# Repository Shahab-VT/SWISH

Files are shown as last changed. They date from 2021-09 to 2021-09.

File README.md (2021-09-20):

# SWISH: A shifting-weight interface of simulated hydrodynamics for haptic perception of virtual fluid vessels

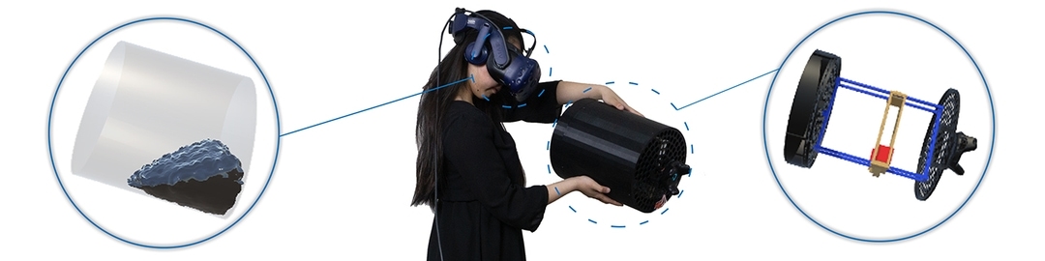
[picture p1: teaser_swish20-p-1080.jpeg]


Publication

Shahabedin Sagheb, Frank Wencheng Liu, Alireza Bahremand, Assegid Kidane, Robert LiKamWa
SWISH: A Shifting-Weight Interface of Simulated Hydrodynamics for Haptic Perception of Virtual Fluid Vessels
In Proceedings of UIST'19: https://dl.acm.org/doi/10.1145/3332165.3347870

Abstract

Current VR/AR systems are unable to reproduce the physical sensation of fluid vessels, due to the shifting nature of fluid motion. To this end, we introduce SWISH, 
an ungrounded mixed-reality interface, capable of affording the users a realistic haptic sensation of fluid behaviors in vessels.The chief mechanism behind SWISH 
is in the use of virtual reality tracking and motor actuation to actively relocate the center of gravity of a handheld vessel, emulating the moving center of 
gravity of a handheld vessel that contains fluid. In addition to solving challenges related to reliable and efficient motor actuation, our SWISH designs place 
an emphasis on reproducibility, scalability, and availability to the maker culture. Our virtual-to-physical coupling uses Nvidia Flex's Unity integration for 
virtual fluid dynamics with a3D printed augmented vessel containing a motorized mechanical actuation system.To evaluate the effectiveness and perceptual 
efficacy of SWISH, we conduct a user study with 24 participants, 7 vessel actions, and 2 virtual fluid viscosities in a virtual reality environment. 
In all cases, the users on average reported that the SWISH bucket generates accurate tactile sensations for the fluid behavior. This opens the potential for 
multi-modal interactions with programmable fluids in virtual environments for chemistry education, worker training, and immersive entertainment.

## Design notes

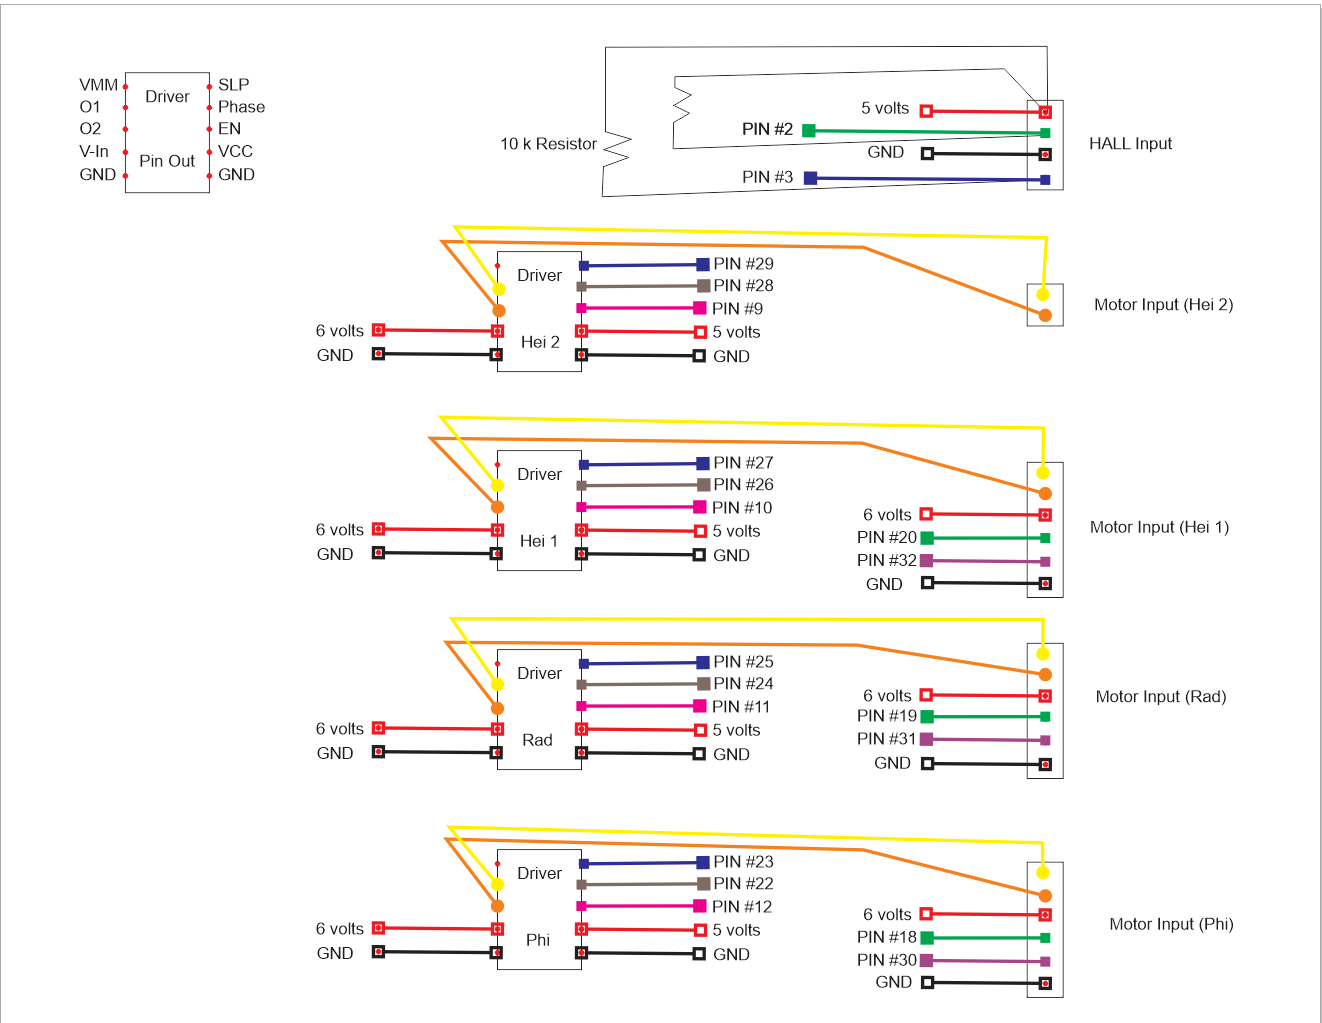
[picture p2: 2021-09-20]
Schematics/SWISH_PCB_1.PNG

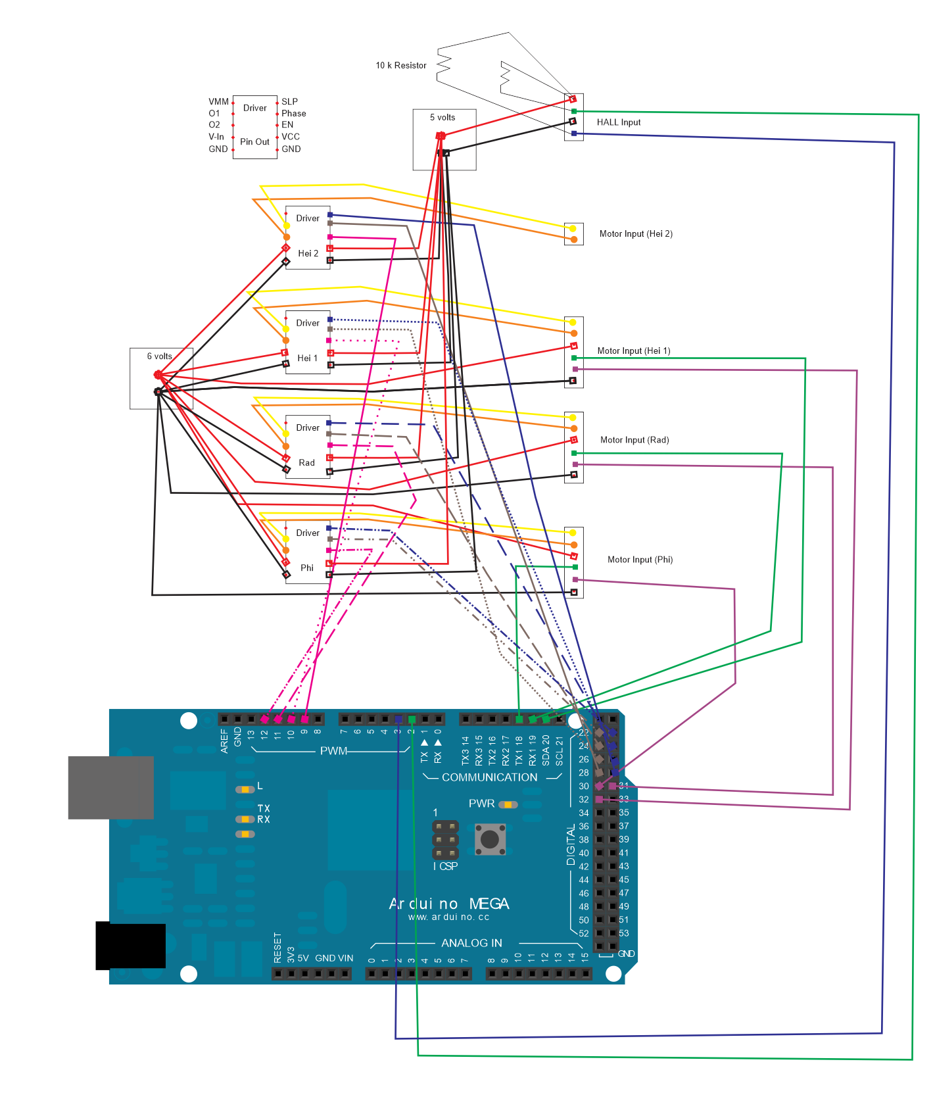
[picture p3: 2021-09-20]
Schematics/SWISH_PCB_2_Wires.PNG

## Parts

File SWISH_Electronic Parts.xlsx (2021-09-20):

Part | Model | Quantity | Link to purchase | Notes
DC Motor | 298:1 Micro Metal | 4 | Pololu - 298:1 Micro Metal Gearmotor HP 6V with Extended Motor Shaft (https://www.pololu.com/product/2218)
Magnetic Encoder |  | 4 | Pololu - Magnetic Encoder Pair Kit with Side-Entry Connector for Micro Metal Gearmotors, 12 CPR, 2.7-18V (https://www.pololu.com/product/4761)
6 Pin Cable | Female JST SH-Style Cable 12cm | 4 | Pololu - 6-Pin Single-Ended Female JST SH-Style Cable 12cm (https://www.pololu.com/product/4762)
Motor Driver | DRV8838 Single | 4 | Pololu - DRV8838 Single Brushed DC Motor Driver Carrier (https://www.pololu.com/product/2990)
Slip Ring | 12.5mm 18 Wires | 1 | Taidacent Small Slip Ring Conductive Ring Miniature Rotating Conductive Slip Ring 2 4 6 8 10 12 24 Road Cap Slip Ring (18 Wire 2A OD 22mm Metal) - - Amazon.com (https://www.amazon.com/Taidacent-Small-Conductive-Miniature-Rotating/dp/B07Y9MLRJN?s=hi) | Plastic one would do as well
Needle Roller Bearing | 1/2" ID, 11/16" OD, 3/8" Width | 1 | INA SCE86 Needle Roller Bearing, Steel Cage, Open End, Inch, 1/2" ID, 11/16" OD, 3/8" Width, 22000rpm Maximum Rotational Speed, 1210lbf Static Load Capacity, 1040lbf Dynamic Load Capacity: Amazon.com: Industrial & Scientific (https://www.amazon.com/gp/product/B00270U27C/ref=ppx_yo_dt_b_asin_title_o01_s00?ie=UTF8&psc=1)
Ball Bearing | R4-2RS (1/4"x5/8"x0.196") | 1 | (10 Pack) PGN - R4-2RS Sealed Ball Bearing - C3-1/4"x5/8"x0.196" - Lubricated - Chrome Steel: Amazon.com: Industrial & Scientific (https://www.amazon.com/PGN-R4-2RS-Sealed-Bearing-Lubricated/dp/B07GT739PV)
Hall-Effect Sensor | AH1815 (Non-Latching) | 2 | Hall-Effect Sensor - AH1815 (Non-Latching) - SEN-14709 - SparkFun Electronics (https://www.sparkfun.com/products/14709)
Set Screw | 1/4" 20 set screw | 1 | Hardware Store
Magnets | 1/4 inch | 2 | 1/4 Inch Neodymium Rare Earth Cube Magnets N52 (64 Pack) (totalelement.com) (https://totalelement.com/collections/cube-magnets/products/1-4-inch-neodymium-rare-earth-cube-magnets-n52-64-pack)
Male & Female Pin Headers |  | N/A | 80 Pieces Male and Female Pin Header Connector 40 Pin 2.54 mm Single Row Straight Pin for Arduino Shield: Amazon.com: Industrial & Scientific (https://www.amazon.com/gp/product/B07VNXL5BD/ref=ppx_yo_dt_b_asin_title_o06_s00?ie=UTF8&psc=1)
Heat Shrink |  | N/A

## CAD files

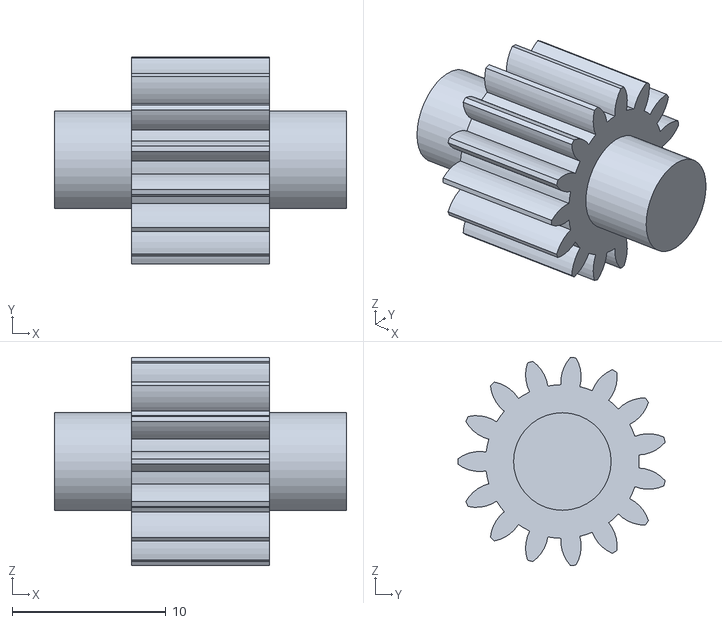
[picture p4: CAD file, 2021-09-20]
STL Files for printing/LASy_SW_spur_gear_Vert_4_Bottom.STL
19.0 x 13.5 x 13.6

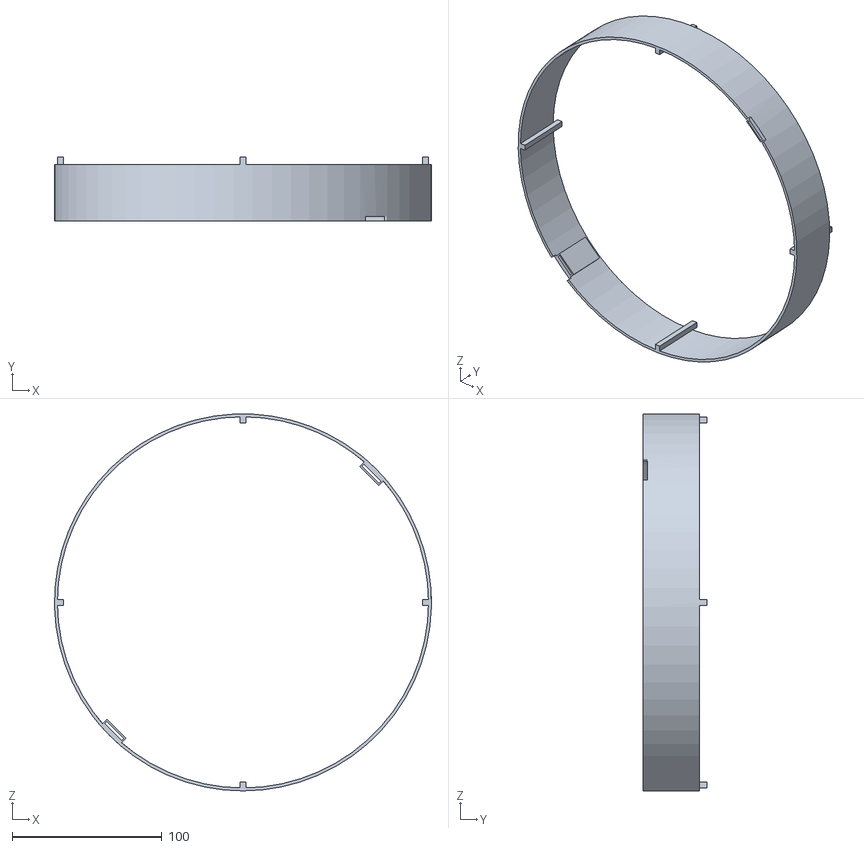
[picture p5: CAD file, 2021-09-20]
STL Files for printing/LASy_Bucket_Stand_3_WiSup.STL
252.0 x 43.0 x 251.8

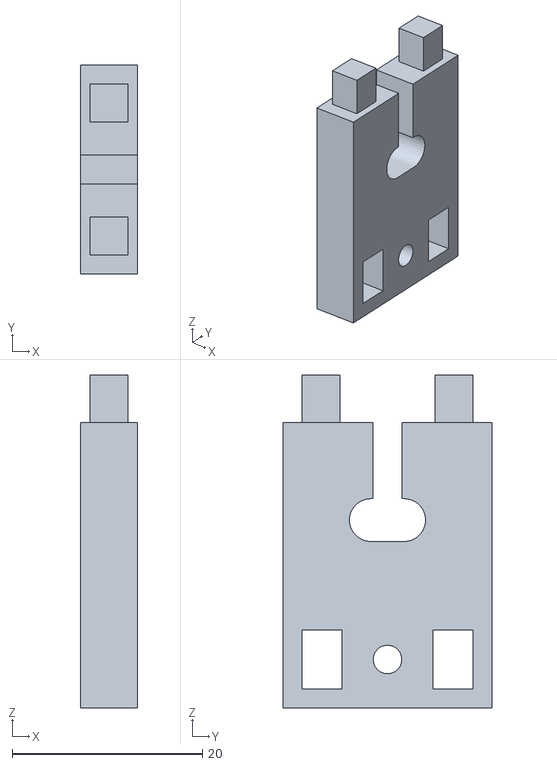
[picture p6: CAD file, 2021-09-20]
STL Files for printing/LASy_Bucket_Top_ViveSupp_Side.STL
6.00 x 22.0 x 35.0

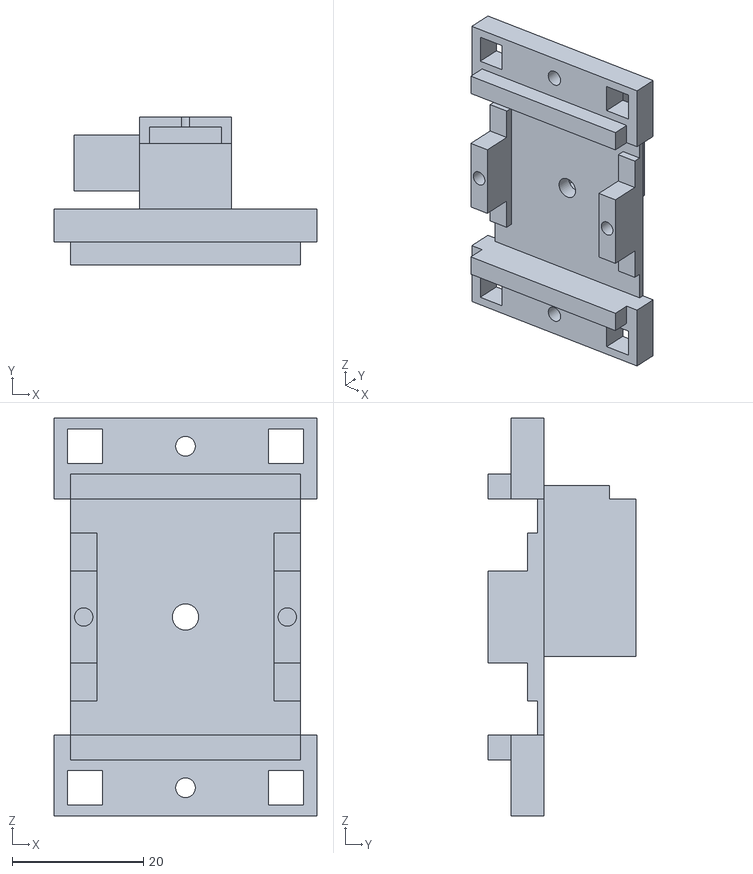
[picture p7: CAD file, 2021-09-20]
STL Files for printing/LASy_SW_Vert_MotorGear_Frame_6_L_SWiS.STL
40.0 x 22.5 x 60.6

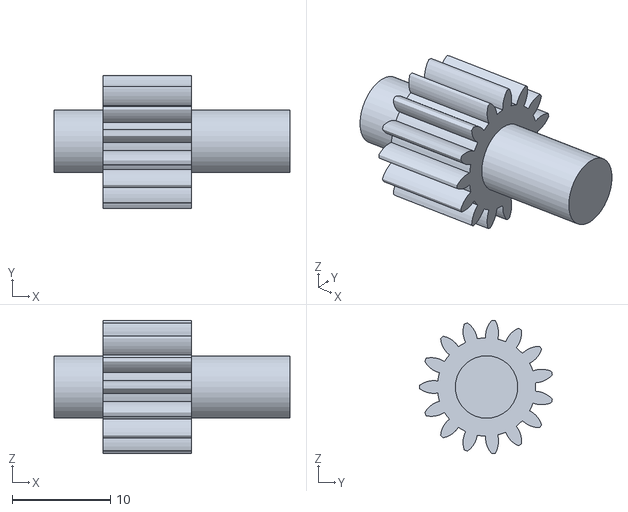
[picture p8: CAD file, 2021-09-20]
STL Files for printing/LASy_SW_spur_gear_Vert_4_1_Bottom_LenMod.STL
24.0 x 13.5 x 13.6

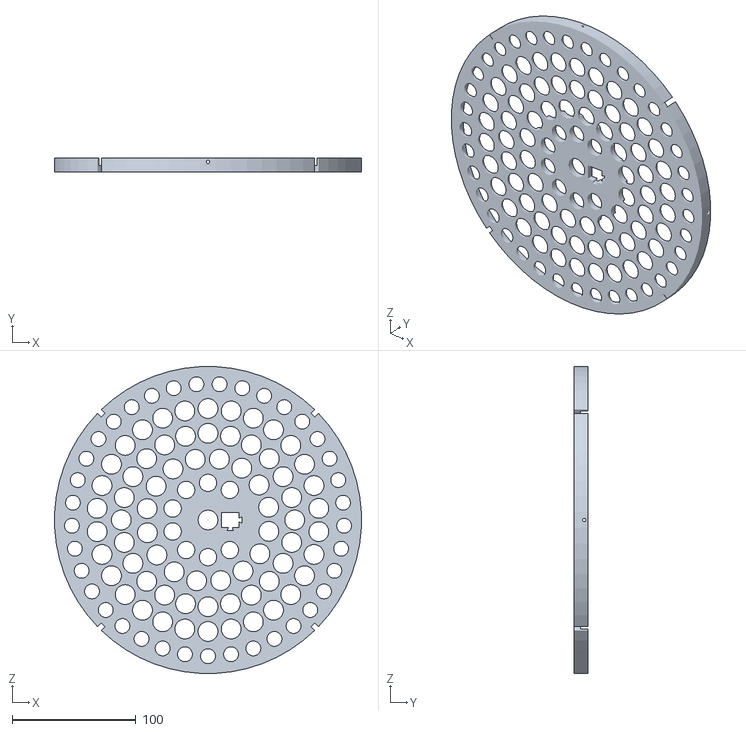
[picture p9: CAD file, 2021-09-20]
STL Files for printing/LASy_Bucket_Bottom.STL
247.9 x 11.0 x 247.9

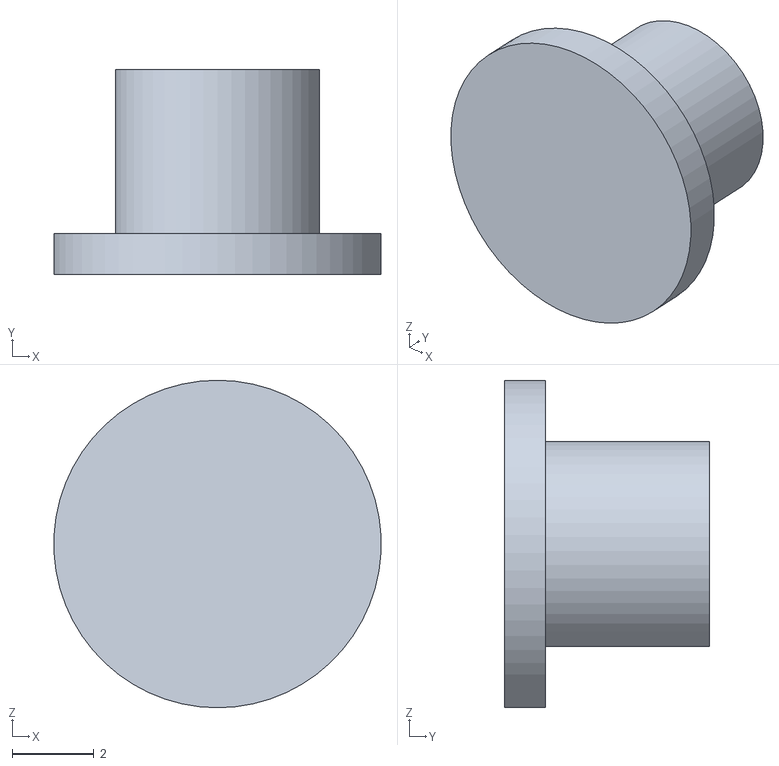
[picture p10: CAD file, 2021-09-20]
STL Files for printing/LASy_Bucket_Top_ViveSupp_Stabilizier.STL
7.99 x 5.00 x 8.00

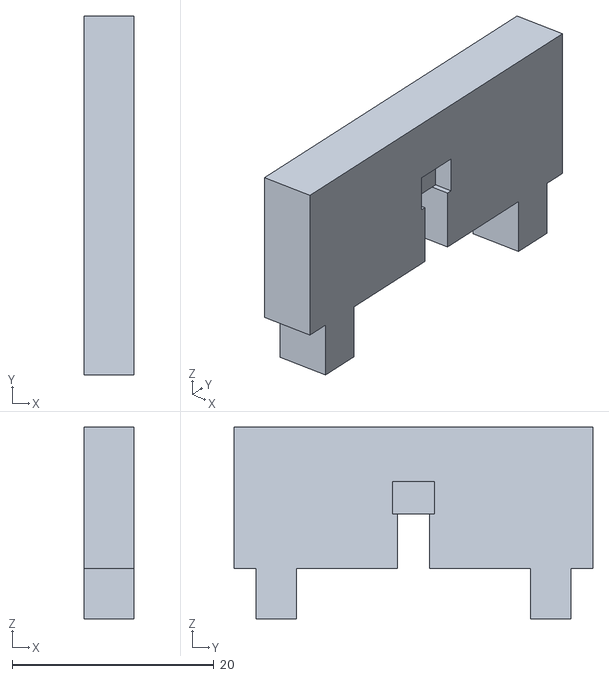
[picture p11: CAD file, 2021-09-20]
STL Files for printing/LASy_SW_V_Rack_Frame_B_Hall_Ext.STL
5.00 x 35.6 x 19.0

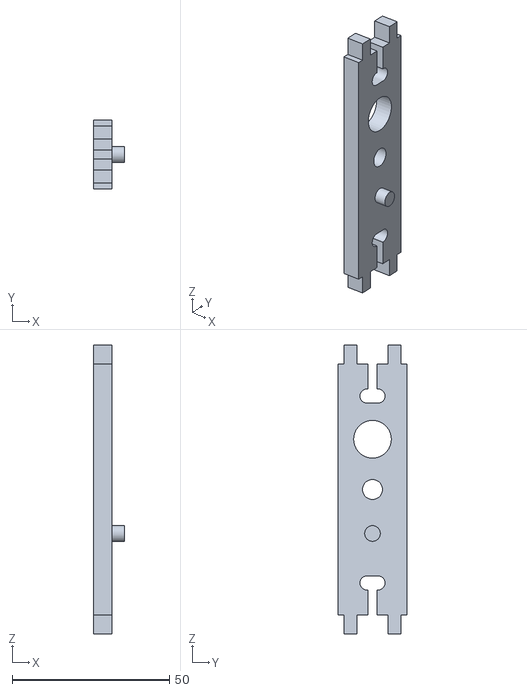
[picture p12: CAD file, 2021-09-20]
STL Files for printing/LASy_Bucket_Top_ViveSupp_1_Stabi.STL
10.0 x 22.0 x 92.0

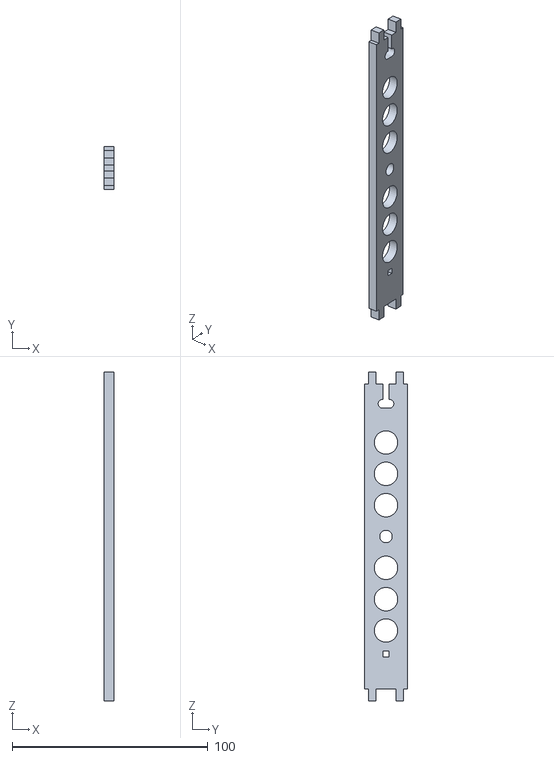
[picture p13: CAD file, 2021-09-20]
STL Files for printing/LASy_SW_V_Rack_Frame_Bott_1_Hall.STL
5.00 x 22.0 x 168.0

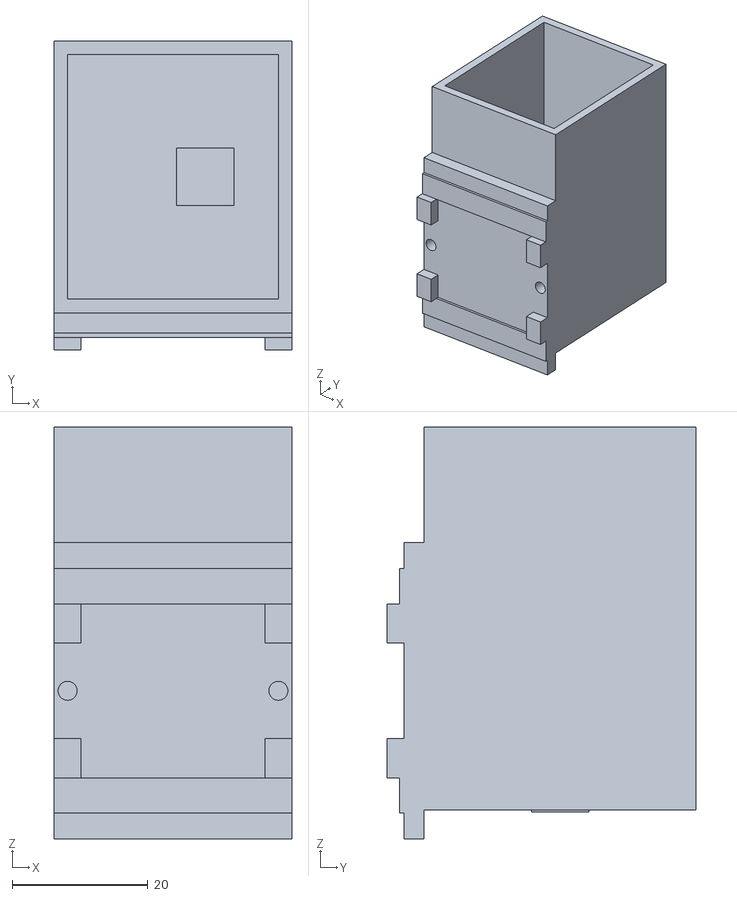
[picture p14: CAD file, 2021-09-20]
STL Files for printing/LASy_SW_H_Motor_Frame_Top_2_Mag_17Taller.STL
35.0 x 45.5 x 60.6

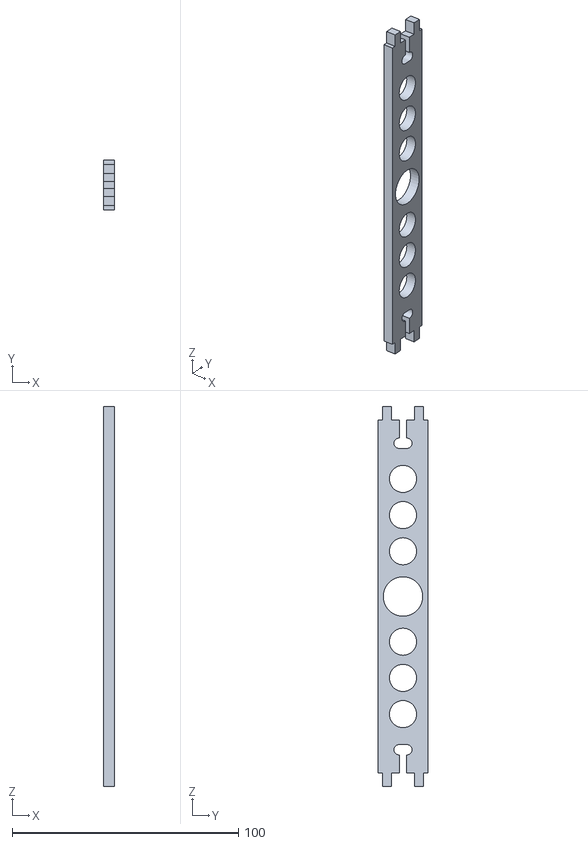
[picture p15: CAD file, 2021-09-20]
STL Files for printing/LASy_SW_V_Rack_Frame_Top.STL
5.00 x 22.0 x 168.0

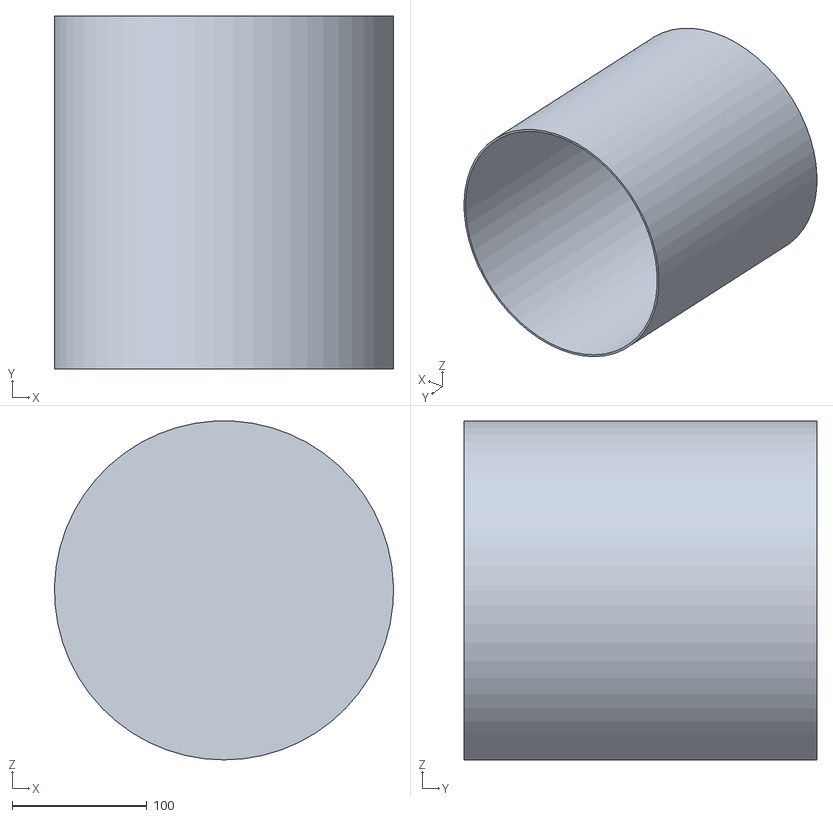
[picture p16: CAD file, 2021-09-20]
STL Files for printing/UserStudy_Bucket_Body.STL
251.9 x 262.0 x 251.8

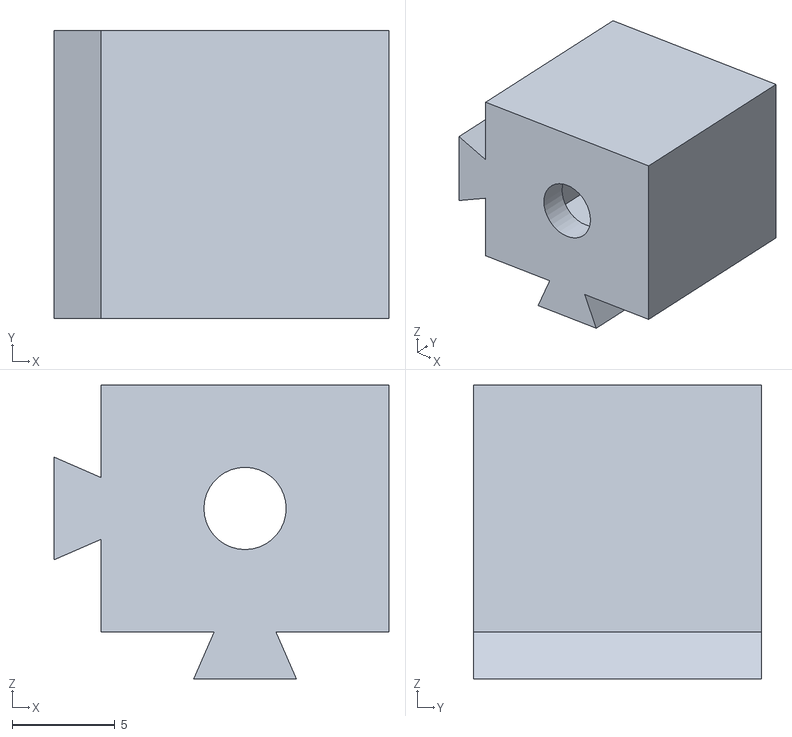
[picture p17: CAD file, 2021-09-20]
STL Files for printing/LASy_SW_Base_Motor_Frame_4.STL
16.3 x 14.0 x 14.3

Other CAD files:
STL Files for printing/LASy_SW_Vert_MotorGear_Frame_7_L_Sq_SWiS.STL
STL Files for printing/LASy_Bucket_Top_ViveSupp_2_Stabi_Snug.STL
STL Files for printing/LASy_SW_Vert_MotorGear_Frame_7_Sq_SWiS.STL
STL Files for printing/LASy_SW_H_Motor_Frame_Top_1_1_MagMod.STL
STL Files for printing/LASy_Bucket_Body.STL
STL Files for printing/LASy_Bucket_Bottom_1_RigFix.STL
STL Files for printing/LASy_Bucket_Stand_2.STL
STL Files for printing/LASy_Bucket_Top.STL
STL Files for printing/LASy_SW_H_Motor_Frame_Top_1_Mag.STL
STL Files for printing/LASy_SW_H_Motor_Frame_Top_2_Mag_34Taller.STL
STL Files for printing/LASy_SW_H_Motor_Frame_Top_Lid.STL
STL Files for printing/LASy_SW_H_Rack.STL
STL Files for printing/LASy_SW_Hori_MotorGear_Frame_2_WiSupp.STL
STL Files for printing/LASy_SW_Hori_MotorGear_Frame_3_Sq_WiSupp.STL
STL Files for printing/LASy_SW_V_Rack_5_WiSupp.STL
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

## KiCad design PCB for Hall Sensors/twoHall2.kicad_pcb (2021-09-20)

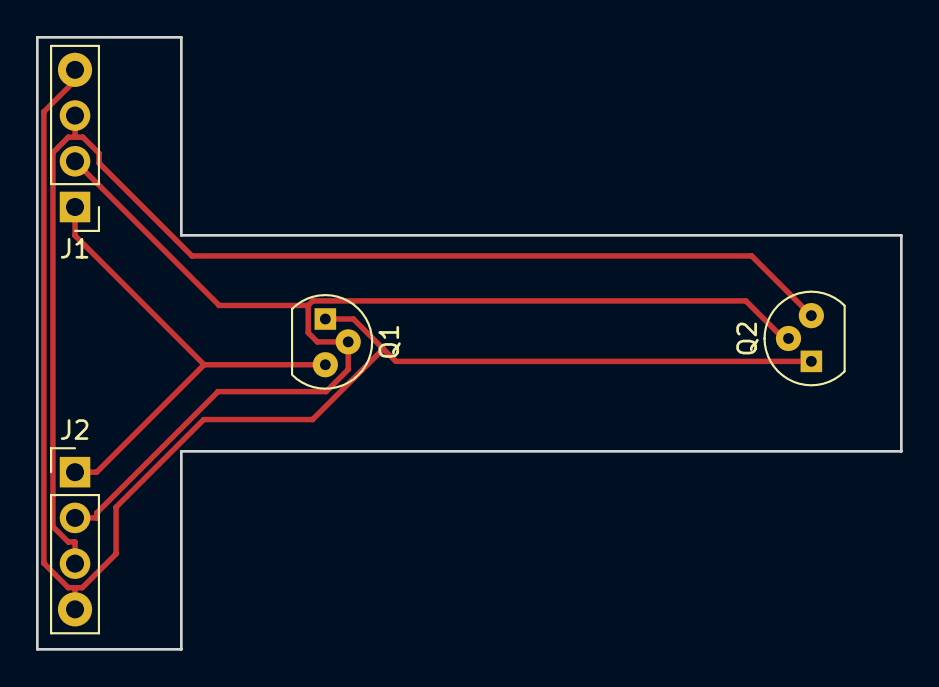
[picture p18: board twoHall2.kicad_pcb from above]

Board: 2 copper layers, 48.0 x 34.0 mm, 4 parts (0 on the bottom side), 4 nets.

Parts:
J1, J2: Conn_01x04; Pin_Header_Straight_1x04_Pitch2.54mm
Q1, Q2: 2N3904; TO-92_Molded_Narrow

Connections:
unnamed: J1.1, J2.1, Q1.3
unnamed: J1.2, J2.2, Q1.2, Q2.2
unnamed: J1.3, J2.3, Q2.3
unnamed: J1.4, J2.4, Q1.1, Q2.1

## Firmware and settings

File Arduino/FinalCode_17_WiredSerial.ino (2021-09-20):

// SWISH2.0 Position control for DC Motors
// For Driver Pololu item #: 2990
// For Encoder Pololu item #: 3081
// The encoders provide a resolution of 12 counts per revolution
// Gear ratio x 12 --> 298 x 12 = 3576 is one rotation
// Gear ratio x 12 --> 1000 x 12 = 12000 is one rotation (1000:1 DC)
// Phi 1 rotation = 1788, Rad Max = 6168, Hei Max = 9015
// Phi range 0 -- -1700

#include <PID_v1.h>      //For calculating PID
#include <Encoder.h>     //For reading ticks of rotary encoder

// Encoder Pins from rotary encoder
#define OUT_phiA    18      // OUT_A needs to be an intrupt pin
#define OUT_phiB    30

#define OUT_radA    19
#define OUT_radB    31

#define OUT_heiA    20
#define OUT_heiB    32


// Pins from motor controller
#define phiPWM_PIN      12  // PWM_PIN is the ENABLE pin on the board
#define phiPHASE_PIN    22  // PHASE is the direction pin
#define phiSLEEP_PIN    23  // SLEEP_PIN is on/off pin on the board

#define radPWM_PIN      11
#define radPHASE_PIN    24
#define radSLEEP_PIN    25

#define hei1PWM_PIN      10
#define hei1PHASE_PIN    26
#define hei1SLEEP_PIN    27

#define hei2PWM_PIN      9
#define hei2PHASE_PIN    28
#define hei2SLEEP_PIN    29

// Pins for Hall sensors (limit switches)
const int interruptPinHei = 3;
const int interruptPinRad = 2;

// Variables not used
bool heiHall = false;
bool radHall = false;

//Initialize limit switch halls
int radhallVal = LOW;
int heihallVal = LOW;



bool startLoop = false;  // To start the loop function when homing is done
bool WRITEBACK = true; // Not used, from an older version   
bool PARSEINT = true; //PARSEINT should be false for Unity, true for testing via Serial Monitor

bool home1 = false; //to start the homing for height
bool radHomeGo = false; // to start homing for radius

// Variables to receive data from serial
int intIn[3];


//Define an instance of encoder
Encoder phiEnc(OUT_phiA, OUT_phiB);  // OUT_A needs to be an intrupt pin
Encoder radEnc(OUT_radA, OUT_radB);
Encoder heiEnc(OUT_heiA, OUT_heiB);


//Define the PID variables
double phiSetpoint, phiInput, phiOutput;
double phivalue = 0;
boolean phi_pid_enable = false;

double radSetpoint, radInput, radOutput;
double radvalue = 0;
boolean rad_pid_enable = false;

double heiSetpoint, heiInput, heiOutput;
double heivalue = 0;
boolean hei_pid_enable = false;


//Specify the links and initial tuning parameters for PID
double phiKp = 0.25, phiKi = 0.0001, phiKd = 0.01;
PID phiPID(&phiInput, &phiOutput, &phiSetpoint, phiKp, phiKi, phiKd, DIRECT);  // if motor will only run at full speed try 'REVERSE' instead of 'DIRECT'

double radKp = 0.25, radKi = 0.0001, radKd = 0.01;
PID radPID(&radInput, &radOutput, &radSetpoint, radKp, radKi, radKd, DIRECT);

double heiKp = 0.25, heiKi = 0.0001, heiKd = 0.01;
PID heiPID(&heiInput, &heiOutput, &heiSetpoint, heiKp, heiKi, heiKd, DIRECT);



void setup() {

  Serial.begin(115200);
//  Serial2.begin(115200);
  


  // Used for no ISR method of limit switches (halls)
  pinMode (interruptPinHei, INPUT);
  pinMode (interruptPinRad, INPUT);


  //PIN Initiation
  pinMode (phiPHASE_PIN, OUTPUT);
  pinMode (phiPWM_PIN, OUTPUT);
  pinMode (phiSLEEP_PIN, OUTPUT);

  pinMode (radPHASE_PIN, OUTPUT);
  pinMode (radPWM_PIN, OUTPUT);
  pinMode (radSLEEP_PIN, OUTPUT);

  pinMode (hei1PHASE_PIN, OUTPUT);
  pinMode (hei1PWM_PIN, OUTPUT);
  pinMode (hei1SLEEP_PIN, OUTPUT);

  pinMode (hei2PHASE_PIN, OUTPUT);
  pinMode (hei2PWM_PIN, OUTPUT);
  pinMode (hei2SLEEP_PIN, OUTPUT);


  //Initialize the variables
  phiInput = phiEnc.read(); // This reads the current position of the rotary encoder
  phiSetpoint = 0;

  radInput = radEnc.read();
  radSetpoint = 0;

  heiInput = heiEnc.read();
  heiSetpoint = 0;


  //Turn the PID on
  phiPID.SetMode(AUTOMATIC);
  phiPID.SetOutputLimits(-255, 255);
  delay(1000);

  radPID.SetMode(AUTOMATIC);
  radPID.SetOutputLimits(-255, 255);
  delay(1000);

  heiPID.SetMode(AUTOMATIC);
  heiPID.SetOutputLimits(-255, 255);
  delay(1000);



  home1 = true;


}




void loop()
{


  heihallVal = digitalRead(interruptPinHei);
  radhallVal = digitalRead(interruptPinRad);

//This is where the homing happens
  if (home1) {
// first home the height
    if (heihallVal != LOW)
    {
      digitalWrite(hei1SLEEP_PIN, HIGH);
      digitalWrite(hei1PHASE_PIN, LOW);
      analogWrite(hei1PWM_PIN, 150);

      digitalWrite(hei2SLEEP_PIN, HIGH);
      digitalWrite(hei2PHASE_PIN, LOW);
      analogWrite(hei2PWM_PIN, 150);
      delay(500);
      heiEnc.write(7000);
      delay(200);
      heiEnc.write(7000);

    }

    if (heihallVal == LOW)
    {
      delay(500);
      heiEnc.write(7000);
      delay(500);
      heiEnc.write(7000);
      radHomeGo = true;
    }

// start homing for radius
    if (radHomeGo)
    {


      if (radhallVal != LOW)
      {
        delay(1000);
        digitalWrite(radSLEEP_PIN, HIGH);
        digitalWrite(radPHASE_PIN, LOW);
        analogWrite(radPWM_PIN, 200);
        delay(500);
        radEnc.write(6000);
        delay(200);
        radEnc.write(6000);
        //Serial.println("radYES");

      }
      if (radhallVal == LOW)

      {
        //Serial.println("radYES");
        home1 = false;
        startLoop = true;
        delay(500);
        radEnc.write(6000);
        delay(200);
        radEnc.write(6000);
        radSetpoint = 3084;
        rad_pid_enable = true;
        delay(50);
        heiEnc.write(7000);
        phiEnc.write(0);
      }
    }
  }
  //delay(1000);

//Homing is done now start listening to numbers from Unity
  if (startLoop)
  {
//PID calculation for theta
    phiInput = phiEnc.read();
    //Serial.print("phi: ");
    //Serial.println(phiInput);
    phiPID.Compute();

    if (phi_pid_enable) {
      phipwmOut(phiOutput);
    }
    else {
      // Put the motor to sleep mode, that is break
      digitalWrite(phiSLEEP_PIN, LOW);
      digitalWrite(phiPHASE_PIN, LOW);
    }

//PID calculation for Radius
    radInput = radEnc.read();
    //Serial.print("rad: ");
    //Serial.println(radInput);
    radPID.Compute();

    if (rad_pid_enable) {
      radpwmOut(radOutput);
    }
    else {
      // Put the motor to sleep mode, that is break
      digitalWrite(radSLEEP_PIN, LOW);
      digitalWrite(radPHASE_PIN, LOW);
    }

//PID calculation for Height
    heiInput = heiEnc.read();
    //Serial.print("hei: ");
    //Serial.println(heiInput);
    heiPID.Compute();

    if (hei_pid_enable) {
      heipwmOut(heiOutput);
      //hei2pwmOut(heiOutput);
    }
    else {
      // Put the motor to sleep mode, that is break
      digitalWrite(hei1SLEEP_PIN, LOW);
      digitalWrite(hei1PHASE_PIN, LOW);
      // digitalWrite(hei2SLEEP_PIN, LOW);
      // digitalWrite(hei2PHASE_PIN, LOW);
    }

//Serial.println("phi:\trad:\thei:");
////Serial.print("\t");
//Serial.print(phiInput);
//Serial.print("\t");
//Serial.print(radInput);
//Serial.print("\t");
//Serial.print(heiInput);
//Serial.println();

//Listen to the port from Unity
    if (Serial.available() > 0) {

//            if (PARSEINT) {
//              for (int x = 0; x < 3; x++)
//              {
//                intIn[x] = Serial.parseInt();
//              }
//            } else {
//              Serial.readBytes((char *)intIn, 6); //Read 6 bytes (3 ints)
//            }


      int len = Serial.readBytes ((char *) intIn, 6);
      
      //if (Serial.read() == '\n') {
      if (len == 6) {
        phiSetpoint = intIn[0];
        radSetpoint = intIn[1];
        heiSetpoint = intIn[2];

        phi_pid_enable = true;
        rad_pid_enable = true;
        hei_pid_enable = true;


      }


      //Report back if WRITEBACK is true, not being used
      if (WRITEBACK) {
        Serial.write((char *)intIn, 6);
      }
    }
  }
}


//send the theta motors at the heighest speed to the specified position
void phipwmOut(int phiOut) {

  if (phiOut < 0) {
    //forward
    digitalWrite(phiSLEEP_PIN, HIGH);
    digitalWrite(phiPHASE_PIN, HIGH);
    analogWrite(phiPWM_PIN, abs(phiOut));
    //Serial.println(phiOut);
  }
  else {
    //backward
    digitalWrite(phiSLEEP_PIN, HIGH);
    digitalWrite(phiPHASE_PIN, LOW);
    analogWrite(phiPWM_PIN, abs(phiOut));
    //Serial.println(phiOut);
  }
}


//send the radius motors at the heighest speed to the specified position
void radpwmOut(int radOut) {

  if (radOut < 0) {
    //forward
    digitalWrite(radSLEEP_PIN, HIGH);
    digitalWrite(radPHASE_PIN, HIGH);
    analogWrite(radPWM_PIN, abs(radOut));
  }
  else {
    //backward
    digitalWrite(radSLEEP_PIN, HIGH);
    digitalWrite(radPHASE_PIN, LOW);
    analogWrite(radPWM_PIN, abs(radOut));
  }
}


//send the height motors at the heighest speed to the specified position
void heipwmOut(int heiOut) {

  if (heiOut < 0) {
    //forward
    digitalWrite(hei1SLEEP_PIN, HIGH);
    digitalWrite(hei1PHASE_PIN, HIGH);
    analogWrite(hei1PWM_PIN, abs(heiOut));
    digitalWrite(hei2SLEEP_PIN, HIGH);
    digitalWrite(hei2PHASE_PIN, HIGH);
    analogWrite(hei2PWM_PIN, abs(heiOut));
  }
  else {
    //backward
    digitalWrite(hei1SLEEP_PIN, HIGH);
    digitalWrite(hei1PHASE_PIN, LOW);
    analogWrite(hei1PWM_PIN, abs(heiOut));
    digitalWrite(hei2SLEEP_PIN, HIGH);
    digitalWrite(hei2PHASE_PIN, LOW);
    analogWrite(hei2PWM_PIN, abs(heiOut));
  }
}

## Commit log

2021-09-20 SWISH Design Files Uploaded
    [LASy_Bucket_Body.STL, LASy_Bucket_Bottom.STL, LASy_Bucket_Bottom_1_RigFix.STL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]
2021-09-20 BOM uploaded
    [SWISH_Electronic Parts.xlsx]
